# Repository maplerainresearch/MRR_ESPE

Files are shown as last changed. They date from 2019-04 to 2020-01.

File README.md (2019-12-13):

# MRR_ESPE
## A 3D printer control board based on ESP32

This is a 3D printer control board based on the ESP32 microcontroller, which comes with built-in WiFi and BlueTooth.

**Current version: v0.5rev1**<br>

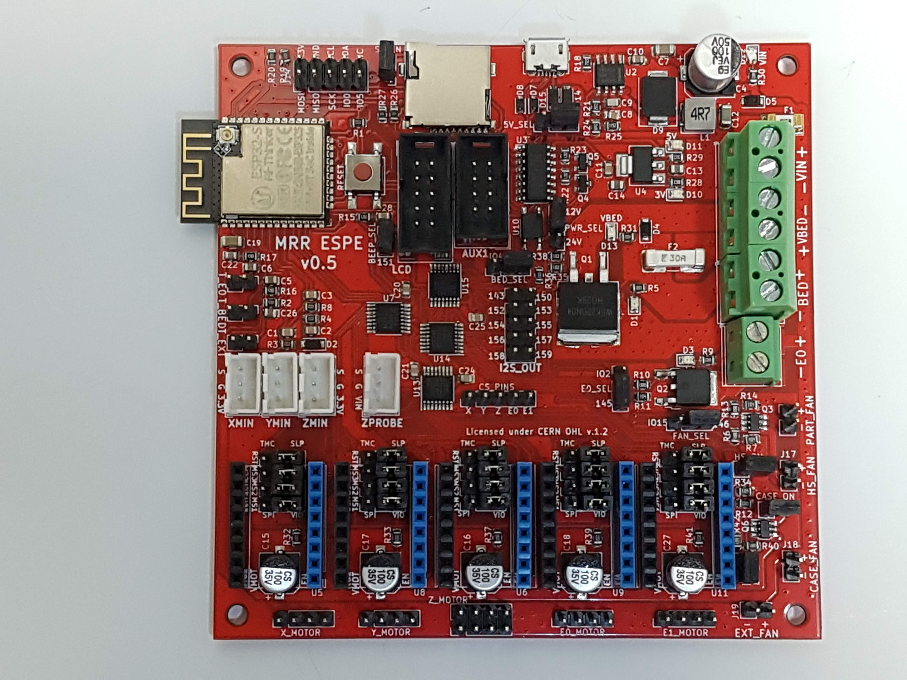
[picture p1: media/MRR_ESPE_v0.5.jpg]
 

Get a pre-launch version at our [store](https://www.maplerain.com/en/products).

Facebook [page](https://www.facebook.com/mrrespx/) <br>
Facebook [group](https://www.facebook.com/groups/mrr.espx.users/) (for discussions, etc.)

Features:
- Able to use up to 5 stepper drivers: X, Y, Z, E0, and E1.
- 12V to 24V input power supply.
- Separate power supply for the heat bed.
- X, Y, and Z min endstops.
- Allows the use of a Z-axis probe, such as an inductive sensor, running on the input supply voltage (12V to 24V).
- Physical size of 102mm by 102mm. Mounting holes are 3.5mm in diameter, with centers 4mm from the edges.
- "RESET" button can be used to reset the board.
- Use of jumper pins for TMC stepper driver connections.
- Firmware controlled fans: case, E0, and EXT. These fans can be controlled by firmware, or they can be in the "always on" mode by shorting the respective jumpers.
- EXP3 connector for Creality LCD controller. 
- AUX1 connector for use with an external host, such as the closed-source MKS TFT32 (**Untested!!**).
- **Note: v0.5 has an issue with AUX1 connector where the RX and TX pins are swapped. To use with controllers like MKS TFT32, dupont connectors will be needed to connect each pin to their corresponding pin separately instead of an IDC cable. The `adapters` directory contains a simple AUX1 adapter board that fixes this issue.**

# Firmware

Marlin 2.0 has added support for ESP32, including the use of I2S to drive motor steppers. This board was based on the pins definition file pins_ESP32.h with some modifications based on MRR ESPA. <br>
In addition, [Luc](https://github.com/luc-github) has been working on a Marlin fork which incorporates part of his ESP3D webUI into Marlin itself.<br>

**Note: Due to timer issues with the I2S stream, babystepping will trigger board reset.**<br>
Note: Marlin's linear advance feature does not work with the I2S stepper stream.<br>

## Flashing firmware

- You should be able to flash firmware through the USB port. Depending on your operating system, you may need to install drivers for the CH340. Please use Google or another search engine to find the right CH340 driver for your operating system.
- To flash firmware by directly connecting to TX/RX pins, you will need to connect IO0 to GND, then reboot (press "BOOT" button) to enter flash mode. After flashing the firmware, disconnect IO0 from GND, and press "BOOT" button again to reboot into normal mode.
- Use a baud rate of 115200.

# Jumpers

- 5V_SEL: Connect to VIN for normal operation; only short (close) this jumper to VUSB if you need to power the board via USB. Note: Powering the board with both PSU and USB may cause unstable operation during heating.
- PWR_SEL: Connect the middle pin PWR_SEL to pin labeled "12V" if using 12V; connect PWR_SEL to pin labeled "24V" if using 24V.
- CASE_ON: Leave open for firmware-controlled case fan; short (close) this jumper for case fan to be always on.
- E0_ON: Leave open for firmware-controlled E0 hotend fan; short (close) this jumper for E0 hotend fan to be always on.
- EXT_ON: Leave open for firmware-controlled extra fan (if used); short (close) this jumper for extra fan to be always on.
- Stepper driver jumpers:
  - MS1: VIO to set high; SPI if using TMC SPI mode
  - MS2: VIO to set high; SPI if using TMC SPI mode
  - MS3: VIO to set high; SPI if using TMC SPI mode
  - RST: SLP if using A4988/DRV8825; SPI if using TMC SPI mode
  - Note: Due to a lack of input pins on the ESP32, UART mode is not supported.

# Pins

See separate PIN_DEF.txt file.
Note: I2S pin 151 labeled as `152` on v0.5 board.

# License
Released under CERN Open Hardware Licence v1.2. See LICENSE.txt for details.

## Warning

- This product uses high currents which may cause fires. Use with caution.
- Do not use input voltages higher than 24V. Input current must not exceed 15A.
- Do not attempt to use more than 15A for the heated bed. While the MOSFET is capable of such currents, the connectors are not. If you need more than 15A, use an external MOSFET. In any case, it is highly recommended to use an external MOSFET for the heated bed to avoid drawing high currents through this product.
- If using a current of more than 10A for the heated bed, it is highly recommended to provide active cooling for the board as the MOSFET and adjacent areas can get very hot due to the high current.
- The underside of the board has PCB traces which are exposed for better cooling. These traces may be carrying high currents and can get very hot. DO NOT touch them, and DO NOT allow these traces to come into contact with metal or other conductive materials.
- Do not attempt to use more than 5A for the hot end. While the MOSFET is capable of such currents, the connectors are not. If you need more than 5A, use an external MOSFET.
- The fan outputs can safely drive up to 0.25A, which is more than enough for most cooling fans. Active cooling of the MOSFETs is recommended for driving currents up to 1A; without active cooling, the MOSFETs can get unduly hot when driving more than 0.25A.
- Do not reverse polarity.
- The breakout and endstop pins are rated for 3.3V, which is the voltage the ESP32 operates at. Attempting to feed inputs above 3.3V to these pins may damage the board.
- It is recommended to power the board only via USB (i.e. turn off PSU power supply) when flashing the board.
- This is still a work in progress. It is recommended not to attempt production using this schematic, although it has been extensively tested.

## Disclaimer

This product is provided as-is. While care has been taken to design a safe product, it is the user's responsibility to make sure precautions are taken to prevent damage or injury when using this product. This includes adhering to all warnings provided. By using this product, the user accepts responsibility to bear all liabilities from any damage or injury arising from the use of this product.

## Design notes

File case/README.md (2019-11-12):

# Cases for MRR ESPE

There are three versions:
1. Basic: Skeleton version, with a simple base, and a top that allows a 40mm fan to be fitted. Standoffs (at least 25mm; more if using stepper drivers with higher heat sinks) are needed.
2. Small: A small, almost enclosed case with a top that allows a 80mm fan to be fitted.
3. Normal: A slightly larger enclosed case, with two types of tops (either a 80mm fan, or two 40mm fans).

There are also covers for 40mm and 80mm fans.

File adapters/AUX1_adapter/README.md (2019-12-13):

# AUX1 adapter
## Fixes issue with AUX1 port on MRR ESPE v0.5

This adapter board fixes MRR ESPE v0.5's issue with the TX/RX pins being swapped on the AUX1 connector.

Simply use an IDC cable to connect AUX1_BRD to the AUX1 connector on the board. Then connect AUX1_SCRN to the screen (such as MKS TFT32).

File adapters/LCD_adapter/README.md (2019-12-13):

# EXP3 to EXP1/2 adapter
## Adapter to allow use of RepRap full graphics smart controller

This adapter allows the MRR ESPE to use generic LCD12864 controllers (officially the RepRap full graphics smart controller).

To do so, connect EXP3_BRD to the LCD connector on the MRR ESPE. Then, connect EXP1 and EXP2 on the adapter to EXP1 and EXP2 on the controller. (Optional: Connect D5, D6, D7 to unused native ESP32 pins on the MRR ESPE, like IO2, IO4, and IO15. Then define `LCD_PINS_D5`, `LCD_PINS_D6`, and `LCD_PINS_D7` in `pins_MRR_ESPE.h`. The KILL pin is also optional.)

If you want to use the SD card on the controller:
1. Remove SD_EN jumper on the MRR ESPE board.
2. Use jumper wires to connect SCK, MISO, and MOSI from the adapter to the respective pins on the board.
3. Connect SS on the adapter to IO5 on the board.
4. Optional: Connect DET to an unused pin on the board. You will need to edit `pins_MRR_ESPE.h` to define the `SD_DETECT_PIN`.

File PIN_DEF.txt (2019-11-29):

Pin Definitions for MRR ESPE
----------------------------

ESP32 pins
0:  BTN_EN1
1:  TX
2:  unused (or HEATER_0_PIN)
3:  RX
4:  unused (or HEATER_BED_PIN)
5:  SS
12: BTN_EN2
13: LCD_PINS_RS
14: BTN_ENC
15: unused (or FAN_PIN)
16: LCD_PINS_D4
17: LCD_PINS_ENABLE
18: SCK
19: MISO
21: SDA
22: SCL
23: MOSI
25: I2S_BCK
26: I2S_WS
27: I2S_DATA
32: Y_MIN_PIN
33: Z_MIN_PIN
34: TEMP_1_PIN
35: X_MIN_PIN
36 (VP): TEMP_E0_PIN
39 (VN): TEMP_BED_PIN

74HC595 (I2S) pins
128: X_ENABLE_PIN
129: X_STEP_PIN
130: X_DIR_PIN
131: Y_ENABLE_PIN
132: Y_STEP_PIN
133: Y_DIR_PIN
134: Z_ENABLE_PIN
135: Z_STEP_PIN
136: Z_DIR_PIN
137: E0_ENABLE_PIN
138: E0_STEP_PIN
139: E0_DIR_PIN
140: E1_ENABLE_PIN
141: E1_STEP_PIN
142: E1_DIR_PIN
143: unused
144: HEATER_BED_PIN
145: HEATER_0_PIN
146: FAN_PIN
147: CONTROLLER_FAN_PIN
148: E0_AUTO_FAN_PIN
149: FAN1_PIN
150: unused
151: BEEPER_PIN
152: unused
153: unused
154: unused
155: unused
156: unused
157: unused
158: unused
159: unused

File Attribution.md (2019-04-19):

# Attribution

Schematics of the following boards were referenced in the design of MRR ESPE:
- [SMART RAMPS 1.42](https://reprap.org/wiki/SMART_RAMPS)
- [ESP32Controller](https://github.com/simon-jouet/ESP32Controller)
- [STEVAL-3DP001V1](https://www.st.com/en/evaluation-tools/steval-3dp001v1.html)
- [Duet 3D Printer Controller](https://github.com/T3P3/Duet)
- [Smoothieboard](https://github.com/Smoothieware/Smoothieboard)
- [Arduino UNO R3](https://www.arduino.cc/en/uploads/Main/Arduino_Uno_Rev3-schematic.pdf)
- [Little-Driver](https://github.com/Digital-Sqrt/Little-Driver)

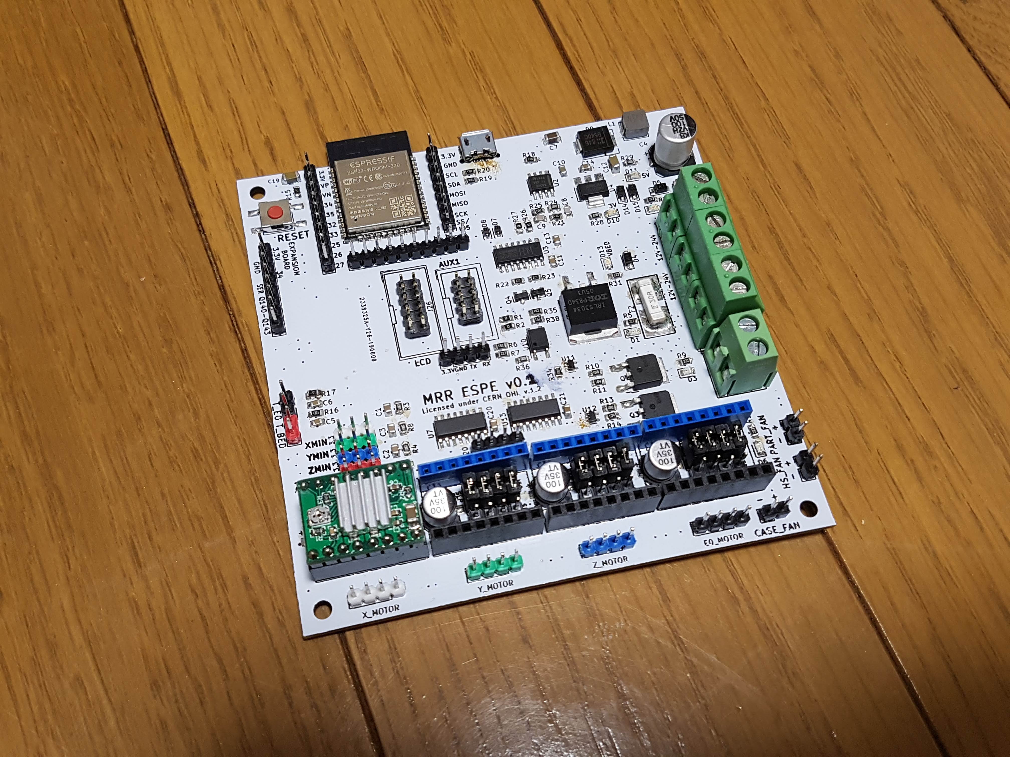
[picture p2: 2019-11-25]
media/MRR_ESPE_v0.2.jpg

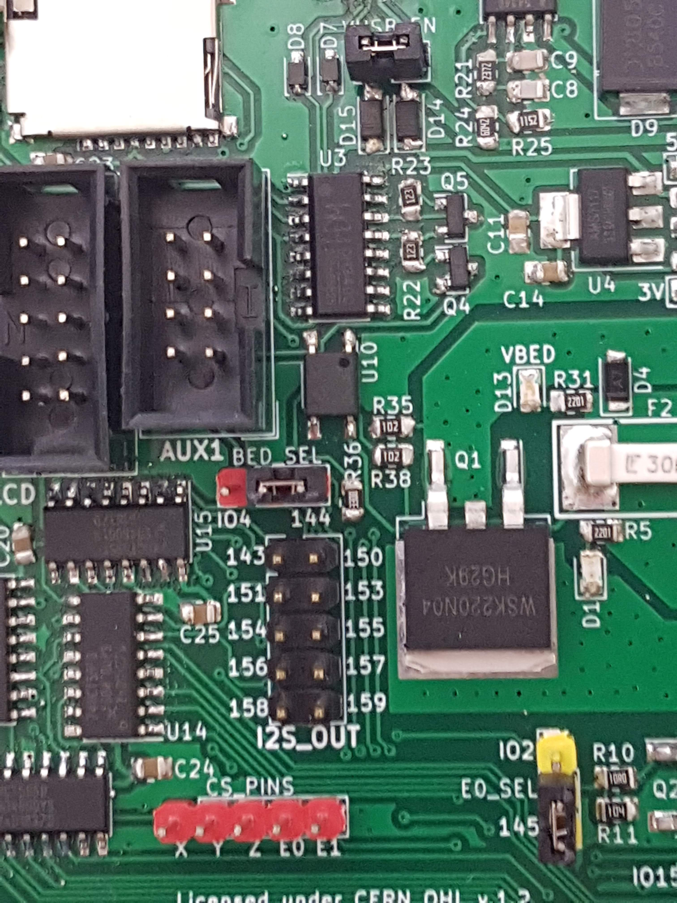
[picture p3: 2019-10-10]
media/ESPE PWM select bed.jpg

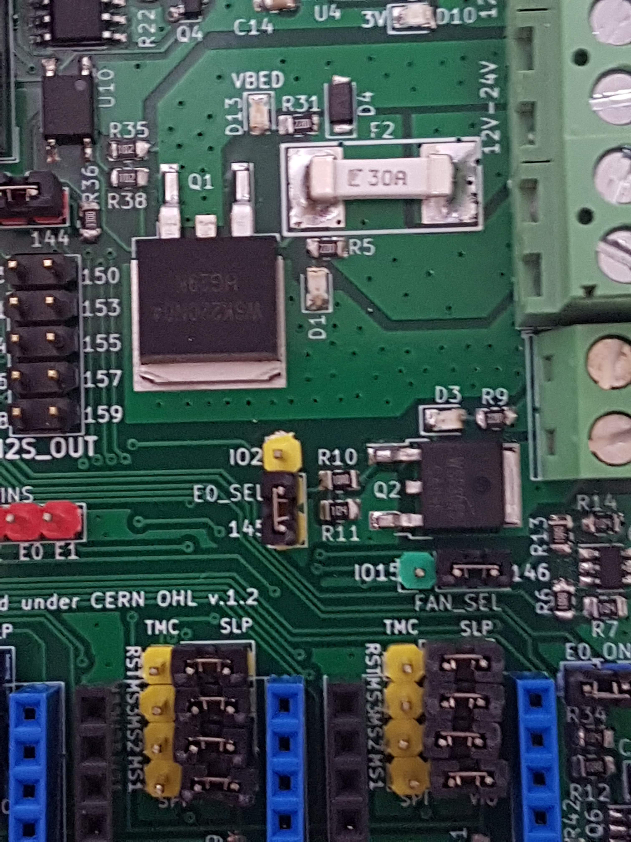
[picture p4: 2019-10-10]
media/ESPE PWM select E0.jpg

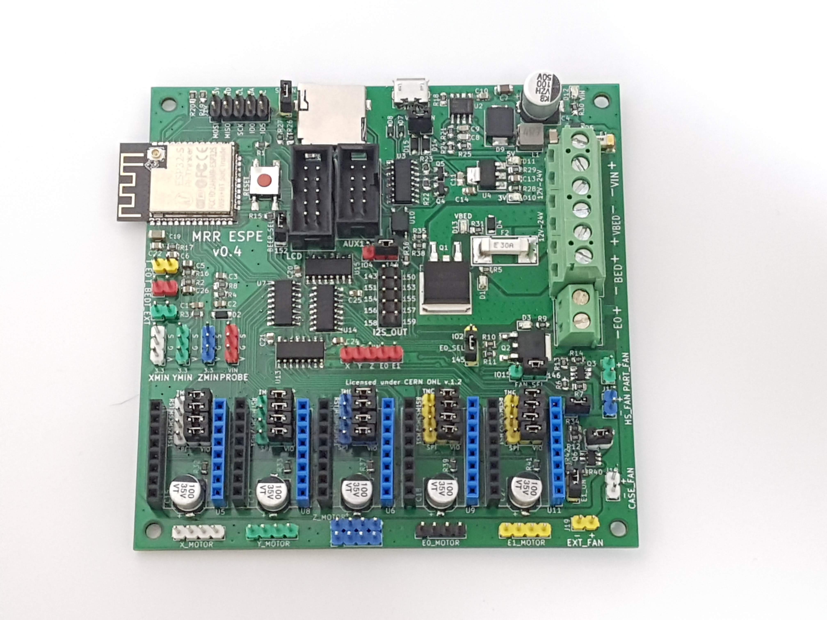
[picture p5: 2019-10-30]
media/MRR_ESPE_v0.4.jpg

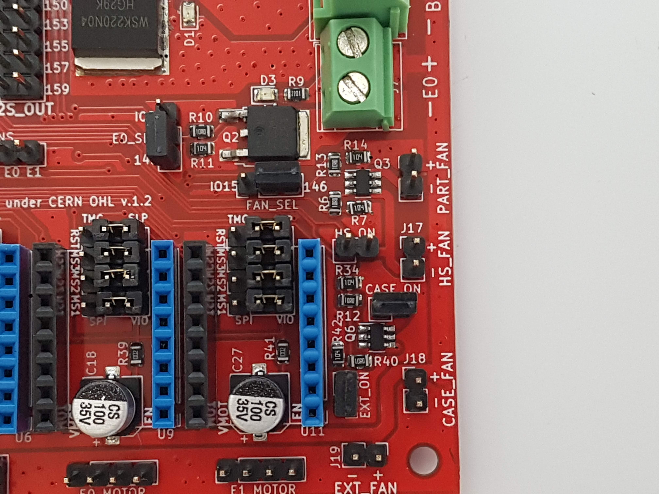
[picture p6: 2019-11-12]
media/ESPE_fan_jumpers.jpg

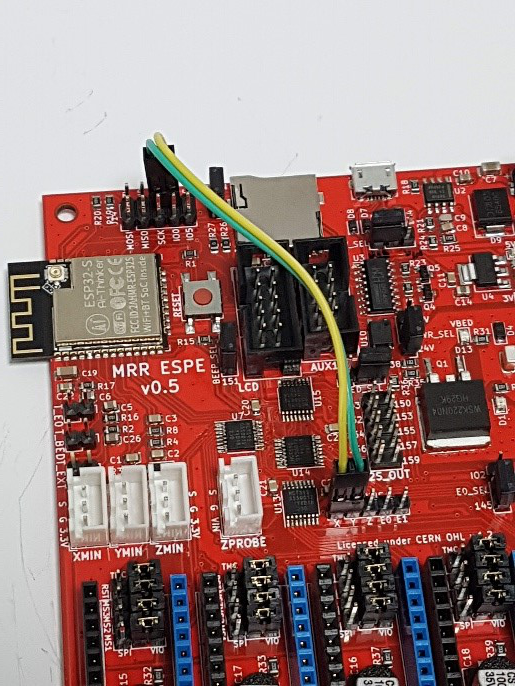
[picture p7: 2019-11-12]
media/ESPE_TMC_jumper_cable.jpg

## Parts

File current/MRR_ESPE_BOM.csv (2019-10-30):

Reference | Value | Footprint | Datasheet | LCSC Part Number | Manufacturer | Mfg part no.
U1 | ESP32-WROOM-32D | RF_Module:ESP32-WROOM-32 | https://www.espressif.com/sites/default/files/documentation/esp32-wroom-32d_esp32-wroom-32u_datasheet_en.pdf | C95209 | Espressif Systems | ESP32-WROOM-32
J9 | PWR_IN | TerminalBlock_Phoenix:TerminalBlock_Phoenix_MKDS-3-4-5.08_1x04_P5.08mm_Horizontal | ~ | C90087 | Phoenix Contact | MKDS3/4-5.08
F1 | 15A 2410 | projfp:Littelfuse_0451 | Bel 0679H9150-01 | C44480 | Littelfuse | 0451015.MRL
F2 | 30A 3912 | projfp:Littelfuse_0456 | Bel 0678H9300-02 | C187558 | Littelfuse | 0456030.ER
D4 | 1N4007W | projfp:D_SOD-123F | http://www.vishay.com/docs/88503/1n4001.pdf | C108803 | Shandong Jingdao Microelectronics | 1N4007W
D5 | 1N4007W | projfp:D_SOD-123F | http://www.vishay.com/docs/88503/1n4001.pdf | C108803 | Shandong Jingdao Microelectronics | 1N4007W
U2 | TPS54340DDA | Package_SO:TI_SO-PowerPAD-8_ThermalVias | http://www.ti.com/lit/ds/symlink/tps54340.pdf | C45886 | Texas Instruments | TPS54340DDAR
C10 | 100nF50V | Capacitor_SMD:C_0805_2012Metric | ~ | C161260 | Murata Electronics | GCM21BR71H104KA37L
C7 | 4.7uF50V | Capacitor_SMD:C_1206_3216Metric | ~ | C307575 | Samsung Electro-Mechanics | CL31B475KBHNFNE
C4 | 100uF50V | Capacitor_SMD:CP_Elec_8x10 | ~ | C176665 | Lelon | VEJ101M1HTR-0810
L1 | 4.7uH4.5A | projfp:SMMS0530 | ~ | C181722 | Shun Xiang Nuo Elec | SMMS0530-4R7M
D9 | B540C-13-F | projfp:D_SMC | ~ | C72264 | Diodes Incorporated | B540C-13-F
R24 | 60.4K | Resistor_SMD:R_0805_2012Metric | ~ | C273994 | YAGEO | RC0805FR-0760K4L
R25 | 11.5K | Resistor_SMD:R_0805_2012Metric | ~ | C17418 | Uniroyal Elec | 0805W8F1152T5E
C12 | 47uF10V | Capacitor_SMD:C_1206_3216Metric | ~ | C92821 | Taiyo Yuden | LMK316BJ476ML-T
C8 | 820pF50V | Capacitor_SMD:C_0805_2012Metric | ~ | C152862 | Walsin Tech Corp | 0805B821K500CT
R21 | 23.7K | Resistor_SMD:R_0805_2012Metric | ~ | C170848 | Walsin Tech Corp | WR08X2372FTL
C9 | 56pF50V | Capacitor_SMD:C_0805_2012Metric | ~ | C296102 | Walsin Tech Corp | 0805N560J500CT
R18 | 73.2K | Resistor_SMD:R_0805_2012Metric | ~ | C170958 | Walsin Tech Corp | WR08X7322FTL
U4 | AMS1117-3.3 | Package_TO_SOT_SMD:SOT-223-3_TabPin2 | http://www.advanced-monolithic.com/pdf/ds1117.pdf | C6186 | Advanced Monolithic Systems | AMS1117-3.3
C14 | 47uF6.3V | Capacitor_SMD:C_0805_2012Metric | ~ | C87159 | Taiyo Yuden | JMK212BJ476MG-T
C13 | 47uF6.3V | Capacitor_SMD:C_0805_2012Metric | ~ | C87159 | Taiyo Yuden | JMK212BJ476MG-T
R28 | 220R | Resistor_SMD:R_0805_2012Metric | ~ | C17557 | Uniroyal Elec | 0805W8F2200T5E
D10 | LED_3V | projfp:LED_0805 | ~ | C73548 | Everlight Elec | 17-21SYGC/S530-E2/TR8
R29 | 330R | Resistor_SMD:R_0805_2012Metric | ~ | C17630 | Uniroyal Elec | 0805W8F3300T5E
R30 | 2.2K | Resistor_SMD:R_0805_2012Metric | ~ | C17520 | Uniroyal Elec | 0805W8F2201T5E
R31 | 2.2K | Resistor_SMD:R_0805_2012Metric | ~ | C17520 | Uniroyal Elec | 0805W8F2201T5E
D11 | LED_5V | projfp:LED_0805 | ~ | C73548 | Everlight Elec | 17-21SYGC/S530-E2/TR8
D12 | LED_VIN | projfp:LED_0805 | ~ | C72035 | Everlight Elec | 17-21/BHC-XL2M2TY/3T
D13 | LED_VBED | projfp:LED_0805 | ~ | C72035 | Everlight Elec | 17-21/BHC-XL2M2TY/3T
R26 | 0R | Resistor_SMD:R_0805_2012Metric | ~ | C17477 | Uniroyal Elec | 0805W8F0000T5E
R27 | 0R | Resistor_SMD:R_0805_2012Metric | ~ | C17477 | Uniroyal Elec | 0805W8F0000T5E
C11 | 1nF16V | Capacitor_SMD:C_0805_2012Metric | ~ | C52278 | Guangdong Fenghua Advanced Tech | 0805B103K500NT
J16 | USB_B_Micro | Connector_USB:USB_Micro-B_Molex-105017-0001 | ~ | C136000 | MOLEX | 105017-0001
D7 | PESD5V0S1BA | projfp:D_SOD-323 | ~ | C19224 | Nexperia | PESD5V0S1BA,115
D8 | PESD5V0S1BA | projfp:D_SOD-323 | ~ | C19224 | Nexperia | PESD5V0S1BA,115
Q4 | S9014 | Package_TO_SOT_SMD:SOT-23 | http://www.onsemi.com/pub_link/Collateral/2N3055-D.PDF | C181164 | Guangdong Hottech | S9014
Q5 | S9014 | Package_TO_SOT_SMD:SOT-23 | http://www.onsemi.com/pub_link/Collateral/2N3055-D.PDF | C181164 | Guangdong Hottech | S9014
R22 | 12K | Resistor_SMD:R_0805_2012Metric | ~ | C17444 | Uniroyal Elec | 0805W8F1202T5E
R23 | 12K | Resistor_SMD:R_0805_2012Metric | ~ | C17444 | Uniroyal Elec | 0805W8F1202T5E
Q1 | IRLS3034PBF | Package_TO_SOT_SMD:TO-263-2 | ~
Q2 | IRLR8743TRPBF | Package_TO_SOT_SMD:TO-252-2 | ~
R5 | 2.2K | Resistor_SMD:R_0805_2012Metric | ~ | C17520 | Uniroyal Elec | 0805W8F2201T5E
D1 | LED_BED | projfp:LED_0805 | ~ | C72037 | Everlight Elec | 17-21SURC/S530-A3/TR8
J3 | BED | TerminalBlock_Phoenix:TerminalBlock_Phoenix_MKDS-3-2-5.08_1x02_P5.08mm_Horizontal | ~ | C89120 | Phoenix Contact | MKDS3/2-5.08
R9 | 2.2K | Resistor_SMD:R_0805_2012Metric | ~ | C17520 | Uniroyal Elec | 0805W8F2201T5E
J7 | E0 | TerminalBlock_Phoenix:TerminalBlock_Phoenix_MKDS-1,5-2-5.08_1x02_P5.08mm_Horizontal | ~ | C91153 | Phoenix Contact | MKDSN1.5/2-5.08
R10 | 10R | Resistor_SMD:R_0805_2012Metric | ~ | C17415 | Uniroyal Elec | 0805W8F100JT5E
R11 | 100K | Resistor_SMD:R_0805_2012Metric | ~ | C149504 | Uniroyal Elec | 0805W8F1003T5E
R13 | 10R | Resistor_SMD:R_0805_2012Metric | ~ | C17415 | Uniroyal Elec | 0805W8F100JT5E
R14 | 100K | Resistor_SMD:R_0805_2012Metric | ~ | C149504 | Uniroyal Elec | 0805W8F1003T5E
J10 | PART_FAN | Connector_PinHeader_2.54mm:PinHeader_1x02_P2.54mm_Vertical | ~ | C124375 | Shenzhen Cankemeng | C124375
U8 | Pololu_board | Module:Pololu_Breakout-16_15.2x20.3mm |  | C27438 | Boom Precision Elec | x2
U5 | Pololu_board | Module:Pololu_Breakout-16_15.2x20.3mm |  | C27438 | Boom Precision Elec | x2
J21 | X_MOTOR | Connector_PinHeader_2.54mm:PinHeader_1x04_P2.54mm_Vertical | ~ | C124378 | Shenzhen Cankemeng | C124378
C15 | 100uF35V | Capacitor_SMD:CP_Elec_6.3x7.7 | ~ | C97811 | Semtech | CS1V101M-CRE77
U6 | Pololu_board | Module:Pololu_Breakout-16_15.2x20.3mm |  | C27438 | Boom Precision Elec | x2
U9 | Pololu_board | Module:Pololu_Breakout-16_15.2x20.3mm |  | C27438 | Boom Precision Elec | x2
C16 | 100uF35V | Capacitor_SMD:CP_Elec_6.3x7.7 | ~ | C97811 | Semtech | CS1V101M-CRE77
C17 | 100uF35V | Capacitor_SMD:CP_Elec_6.3x7.7 | ~ | C97811 | Semtech | CS1V101M-CRE77
C18 | 100uF35V | Capacitor_SMD:CP_Elec_6.3x7.7 | ~ | C97811 | Semtech | CS1V101M-CRE77
J23 | Y_MOTOR | Connector_PinHeader_2.54mm:PinHeader_1x04_P2.54mm_Vertical | ~ | C124378 | Shenzhen Cankemeng | C124378
J24 | E0_MOTOR | Connector_PinHeader_2.54mm:PinHeader_1x04_P2.54mm_Vertical | ~ | C124378 | Shenzhen Cankemeng | C124378
J22 | Z_MOTOR | Connector_PinHeader_2.54mm:PinHeader_2x04_P2.54mm_Vertical | ~ | C124386 | Shenzhen Cankemeng | C124386
D3 | LED_E0 | projfp:LED_0805 | ~ | C72037 | Everlight Elec | 17-21SURC/S530-A3/TR8
J12 | T_BED | Connector_PinHeader_2.54mm:PinHeader_1x02_P2.54mm_Vertical | ~ | C124375 | Shenzhen Cankemeng | C124375
R16 | 4.7K | Resistor_SMD:R_0805_2012Metric | ~ | C17673 | Uniroyal Elec | 0805W8F4701T5E
C5 | 22uF6.3V | Capacitor_SMD:C_0805_2012Metric | ~ | C5674 | Samsung Electro-Mechanics | CL21A226MQQNNNE
J13 | T_E0 | Connector_PinHeader_2.54mm:PinHeader_1x02_P2.54mm_Vertical | ~ | C124375 | Shenzhen Cankemeng | C124375
R17 | 4.7K | Resistor_SMD:R_0805_2012Metric | ~ | C17673 | Uniroyal Elec | 0805W8F4701T5E
C6 | 22uF6.3V | Capacitor_SMD:C_0805_2012Metric | ~ | C5674 | Samsung Electro-Mechanics | CL21A226MQQNNNE
J1 | X_MIN | Connector_JST:JST_XH_B03B-XH-A_1x03_P2.50mm_Vertical | ~ | C144394 | JST Sales America | B3B-XH-A(LF)(SN)
R3 | 10K | Resistor_SMD:R_0805_2012Metric | ~ | C38522 | Uniroyal Elec | 0805W8F1002T5E
C1 | 100nF25V | Capacitor_SMD:C_0805_2012Metric | ~ | C128353 | Walsin Tech Corp | 0805B104K250
J5 | Y_MIN | Connector_JST:JST_XH_B03B-XH-A_1x03_P2.50mm_Vertical | ~ | C144394 | JST Sales America | B3B-XH-A(LF)(SN)
R8 | 10K | Resistor_SMD:R_0805_2012Metric | ~ | C38522 | Uniroyal Elec | 0805W8F1002T5E
C3 | 100nF25V | Capacitor_SMD:C_0805_2012Metric | ~ | C128353 | Walsin Tech Corp | 0805B104K250
J2 | Z_MIN | Connector_JST:JST_XH_B03B-XH-A_1x03_P2.50mm_Vertical | ~ | C144394 | JST Sales America | B3B-XH-A(LF)(SN)
R4 | 10K | Resistor_SMD:R_0805_2012Metric | ~ | C38522 | Uniroyal Elec | 0805W8F1002T5E
C2 | 100nF25V | Capacitor_SMD:C_0805_2012Metric | ~ | C128353 | Walsin Tech Corp | 0805B104K250
J6 | Z_PROBE | Connector_JST:JST_XH_B03B-XH-A_1x03_P2.50mm_Vertical | ~ | C144394 | JST Sales America | B3B-XH-A(LF)(SN)
D2 | 1N4148W | projfp:D_SOD-123 | https://www.vishay.com/docs/85748/1n4148w.pdf | C81598 | Semtech | 1N4148W
R15 | 12K | Resistor_SMD:R_0805_2012Metric | ~ | C17444 | Uniroyal Elec | 0805W8F1202T5E
SW1 | RESET | projfp:6x6mmTactileSwitch |  | C83206 | Korean Hroparts Elec | K2-6639SP-C4SC-04
J15 | AUX1 | Connector_IDC:IDC-Header_2x04_P2.54mm_Vertical | ~ | C9135 | Boom Precision Elec | C9135
R19 | 4.7K | Resistor_SMD:R_0805_2012Metric | ~ | C17673 | Uniroyal Elec | 0805W8F4701T5E
R20 | 4.7K | Resistor_SMD:R_0805_2012Metric | ~ | C17673 | Uniroyal Elec | 0805W8F4701T5E
H1 | MountingHole | MountingHole:MountingHole_3.2mm_M3_DIN965 | ~
H2 | MountingHole | MountingHole:MountingHole_3.2mm_M3_DIN965 | ~
H3 | MountingHole | MountingHole:MountingHole_3.2mm_M3_DIN965 | ~
H4 | MountingHole | MountingHole:MountingHole_3.2mm_M3_DIN965 | ~
JP1 | X_MS1 | Connector_PinHeader_2.54mm:PinHeader_1x03_P2.54mm_Vertical | ~ | C124376 | Shenzhen Cankemeng | C124376
JP5 | X_MS2 | Connector_PinHeader_2.54mm:PinHeader_1x03_P2.54mm_Vertical | ~ | C124376 | Shenzhen Cankemeng | C124376
JP9 | X_MS3 | Connector_PinHeader_2.54mm:PinHeader_1x03_P2.54mm_Vertical | ~ | C124376 | Shenzhen Cankemeng | C124376
JP13 | X_RST | Connector_PinHeader_2.54mm:PinHeader_1x03_P2.54mm_Vertical | ~ | C124376 | Shenzhen Cankemeng | C124376
J20 | CS_PINS | Connector_PinHeader_2.54mm:PinHeader_1x05_P2.54mm_Vertical | ~ | C124379 | Shenzhen Cankemeng | C124379
JP2 | Y_MS1 | Connector_PinHeader_2.54mm:PinHeader_1x03_P2.54mm_Vertical | ~ | C124376 | Shenzhen Cankemeng | C124376
JP6 | Y_MS2 | Connector_PinHeader_2.54mm:PinHeader_1x03_P2.54mm_Vertical | ~ | C124376 | Shenzhen Cankemeng | C124376
JP10 | Y_MS3 | Connector_PinHeader_2.54mm:PinHeader_1x03_P2.54mm_Vertical | ~ | C124376 | Shenzhen Cankemeng | C124376
JP14 | Y_RST | Connector_PinHeader_2.54mm:PinHeader_1x03_P2.54mm_Vertical | ~ | C124376 | Shenzhen Cankemeng | C124376
JP3 | Z_MS1 | Connector_PinHeader_2.54mm:PinHeader_1x03_P2.54mm_Vertical | ~ | C124376 | Shenzhen Cankemeng | C124376
JP7 | Z_MS2 | Connector_PinHeader_2.54mm:PinHeader_1x03_P2.54mm_Vertical | ~ | C124376 | Shenzhen Cankemeng | C124376
JP11 | Z_MS3 | Connector_PinHeader_2.54mm:PinHeader_1x03_P2.54mm_Vertical | ~ | C124376 | Shenzhen Cankemeng | C124376
JP15 | Z_RST | Connector_PinHeader_2.54mm:PinHeader_1x03_P2.54mm_Vertical | ~ | C124376 | Shenzhen Cankemeng | C124376
JP4 | E0_MS1 | Connector_PinHeader_2.54mm:PinHeader_1x03_P2.54mm_Vertical | ~ | C124376 | Shenzhen Cankemeng | C124376
JP8 | E0_MS2 | Connector_PinHeader_2.54mm:PinHeader_1x03_P2.54mm_Vertical | ~ | C124376 | Shenzhen Cankemeng | C124376
JP12 | E0_MS3 | Connector_PinHeader_2.54mm:PinHeader_1x03_P2.54mm_Vertical | ~ | C124376 | Shenzhen Cankemeng | C124376
JP16 | E0_RST | Connector_PinHeader_2.54mm:PinHeader_1x03_P2.54mm_Vertical | ~ | C124376 | Shenzhen Cankemeng | C124376
U3 | CH340C | Package_SO:SOIC-16_3.9x9.9mm_P1.27mm | http://www.datasheet5.com/pdf-local-2195953 | C84681 | Jiangsu Qin Heng | CH340C
J4 | Micro_SD_Card_China | projfp:Conn_uSDcard |  | C111196 | SOFNG | TF-15×15
C19 | 100uF6.3V | Capacitor_SMD:C_1206_3216Metric | ~ | C15008 | Samsung Electro-Mechanics | CL31A107MQHNNNE
R38 | 1K | Resistor_SMD:R_0805_2012Metric | ~ | C17513 | Uniroyal Elec | 0805W8F1001T5E
R35 | 1K | Resistor_SMD:R_0805_2012Metric | ~ | C17513 | Uniroyal Elec | 0805W8F1001T5E
U10 | TLP182 | Package_SO:MFSOP6-4_4.4x3.6mm_P1.27mm | https://toshiba.semicon-storage.com/info/docget.jsp?did=11793&prodName=TLP184 | C96457 | TOSHIBA | TLP182(GB-TPL,E
R36 | 330R | Resistor_SMD:R_0805_2012Metric | ~ | C17630 | Uniroyal Elec | 0805W8F3300T5E
D14 | 1N5819W | Diode_SMD:D_SOD-123 | http://www.vishay.com/docs/88525/1n5817.pdf | C169540 | Shandong Jingdao Microelectronics | 1N5819W
D15 | 1N5819W | Diode_SMD:D_SOD-123 | http://www.vishay.com/docs/88525/1n5817.pdf | C169540 | Shandong Jingdao Microelectronics | 1N5819W
U7 | 74HCT595 | Package_SO:TSSOP-16_4.4x5mm_P0.65mm | http://www.ti.com/lit/ds/symlink/sn74hc595.pdf | C152276 | ON Semicon | MC74HCT595ADTR2G
U13 | 74HCT595 | Package_SO:TSSOP-16_4.4x5mm_P0.65mm | http://www.ti.com/lit/ds/symlink/sn74hc595.pdf | C152276 | ON Semicon | MC74HCT595ADTR2G
C20 | 100nF25V | Capacitor_SMD:C_0805_2012Metric | ~ | C128353 | Walsin Tech Corp | 0805B104K250
C21 | 100nF25V | Capacitor_SMD:C_0805_2012Metric | ~ | C128353 | Walsin Tech Corp | 0805B104K250
J26 | EXP3 | Connector_IDC:IDC-Header_2x05_P2.54mm_Vertical | ~ | C5665 | Boom Precision Elec | C5665
U14 | 74HCT595 | Package_SO:TSSOP-16_4.4x5mm_P0.65mm | http://www.ti.com/lit/ds/symlink/sn74hc595.pdf | C152276 | ON Semicon | MC74HCT595ADTR2G
U15 | 74HCT595 | Package_SO:TSSOP-16_4.4x5mm_P0.65mm | http://www.ti.com/lit/ds/symlink/sn74hc595.pdf | C152276 | ON Semicon | MC74HCT595ADTR2G
C24 | 100nF25V | Capacitor_SMD:C_0805_2012Metric | ~ | C128353 | Walsin Tech Corp | 0805B104K250
C25 | 100nF25V | Capacitor_SMD:C_0805_2012Metric | ~ | C128353 | Walsin Tech Corp | 0805B104K250
C22 | 22uF6.3V | Capacitor_SMD:C_0805_2012Metric | ~ | C5674 | Samsung Electro-Mechanics | CL21A226MQQNNNE
C23 | 100nF25V | Capacitor_SMD:C_0805_2012Metric | ~ | C128353 | Walsin Tech Corp | 0805B104K250
R33 | 10K | Resistor_SMD:R_0805_2012Metric | ~ | C38522 | Uniroyal Elec | 0805W8F1002T5E
R32 | 10K | Resistor_SMD:R_0805_2012Metric | ~ | C38522 | Uniroyal Elec | 0805W8F1002T5E
R37 | 10K | Resistor_SMD:R_0805_2012Metric | ~ | C38522 | Uniroyal Elec | 0805W8F1002T5E
R39 | 10K | Resistor_SMD:R_0805_2012Metric | ~ | C38522 | Uniroyal Elec | 0805W8F1002T5E
R1 | 10K | Resistor_SMD:R_0805_2012Metric | ~ | C38522 | Uniroyal Elec | 0805W8F1002T5E
Q6 | WST3392 | Package_TO_SOT_SMD:SOT-23-6_Handsoldering |  | C148366 | Winsok Semicon | WST3392
Q3 | WST3392 | Package_TO_SOT_SMD:SOT-23-6_Handsoldering |  | C148366 | Winsok Semicon | WST3392
J11 | UNUSED | Connector_PinHeader_2.54mm:PinHeader_2x05_P2.54mm_Vertical | ~ | C124387 | Shenzhen Cankemeng | C124387
R12 | 10R | Resistor_SMD:R_0805_2012Metric | ~ | C17415 | Uniroyal Elec | 0805W8F100JT5E
R34 | 100K | Resistor_SMD:R_0805_2012Metric | ~ | C149504 | Uniroyal Elec | 0805W8F1003T5E
J18 | CASE_FAN | Connector_PinHeader_2.54mm:PinHeader_1x02_P2.54mm_Vertical | ~ | C124375 | Shenzhen Cankemeng | C124375
JP23 | CASE_ON | Connector_PinHeader_2.54mm:PinHeader_1x02_P2.54mm_Vertical | ~ | C124375 | Shenzhen Cankemeng | C124375
R6 | 10R | Resistor_SMD:R_0805_2012Metric | ~ | C17415 | Uniroyal Elec | 0805W8F100JT5E
R7 | 100K | Resistor_SMD:R_0805_2012Metric | ~ | C149504 | Uniroyal Elec | 0805W8F1003T5E
J17 | HS_FAN | Connector_PinHeader_2.54mm:PinHeader_1x02_P2.54mm_Vertical | ~ | C124375 | Shenzhen Cankemeng | C124375
JP21 | HS_ON | Connector_PinHeader_2.54mm:PinHeader_1x02_P2.54mm_Vertical | ~ | C124375 | Shenzhen Cankemeng | C124375
R40 | 10R | Resistor_SMD:R_0805_2012Metric | ~ | C17415 | Uniroyal Elec | 0805W8F100JT5E
R42 | 100K | Resistor_SMD:R_0805_2012Metric | ~ | C149504 | Uniroyal Elec | 0805W8F1003T5E
J19 | EXT_FAN | Connector_PinHeader_2.54mm:PinHeader_1x02_P2.54mm_Vertical | ~ | C124375 | Shenzhen Cankemeng | C124375
JP24 | EXT_ON | Connector_PinHeader_2.54mm:PinHeader_1x02_P2.54mm_Vertical | ~ | C124375 | Shenzhen Cankemeng | C124375
J8 | T_EXT | Connector_PinHeader_2.54mm:PinHeader_1x02_P2.54mm_Vertical | ~ | C124375 | Shenzhen Cankemeng | C124375
R2 | 4.7K | Resistor_SMD:R_0805_2012Metric | ~ | C17673 | Uniroyal Elec | 0805W8F4701T5E
C26 | 22uF6.3V | Capacitor_SMD:C_0805_2012Metric | ~ | C5674 | Samsung Electro-Mechanics | CL21A226MQQNNNE
J14 | I2C/SPI | Connector_PinHeader_2.54mm:PinHeader_2x05_P2.54mm_Vertical | ~ | C124387 | Shenzhen Cankemeng | C124387
JP22 | E1_MS1 | Connector_PinHeader_2.54mm:PinHeader_1x03_P2.54mm_Vertical | ~ | C124376 | Shenzhen Cankemeng | C124376
JP25 | E1_MS2 | Connector_PinHeader_2.54mm:PinHeader_1x03_P2.54mm_Vertical | ~ | C124376 | Shenzhen Cankemeng | C124376
JP26 | E1_MS3 | Connector_PinHeader_2.54mm:PinHeader_1x03_P2.54mm_Vertical | ~ | C124376 | Shenzhen Cankemeng | C124376
JP27 | E1_RST | Connector_PinHeader_2.54mm:PinHeader_1x03_P2.54mm_Vertical | ~ | C124376 | Shenzhen Cankemeng | C124376
U11 | Pololu_board | Module:Pololu_Breakout-16_15.2x20.3mm |  | C27438 | Boom Precision Elec | x2
C27 | 100uF35V | Capacitor_SMD:CP_Elec_6.3x7.7 | ~ | C97811 | Semtech | CS1V101M-CRE77
J25 | E1_MOTOR | Connector_PinHeader_2.54mm:PinHeader_1x04_P2.54mm_Vertical | ~ | C124378 | Shenzhen Cankemeng | C124378
JP18 | BED_SEL | Connector_PinHeader_2.54mm:PinHeader_1x03_P2.54mm_Vertical | ~ | C124376 | Shenzhen Cankemeng | C124376
JP20 | E0_SEL | Connector_PinHeader_2.54mm:PinHeader_1x03_P2.54mm_Vertical | ~ | C124376 | Shenzhen Cankemeng | C124376
JP19 | FAN_SEL | Connector_PinHeader_2.54mm:PinHeader_1x03_P2.54mm_Vertical | ~ | C124376 | Shenzhen Cankemeng | C124376
JP17 | BEEP_SEL | Connector_PinHeader_2.54mm:PinHeader_1x02_P2.54mm_Vertical | ~ | C124375 | Shenzhen Cankemeng | C124375
R41 | 10K | Resistor_SMD:R_0805_2012Metric | ~ | C38522 | Uniroyal Elec | 0805W8F1002T5E
JP29 | SD_EN | Connector_PinHeader_2.54mm:PinHeader_1x02_P2.54mm_Vertical | ~ | C124375 | Shenzhen Cankemeng | C124375
JP30 | PWR_SEL | Connector_PinHeader_2.54mm:PinHeader_1x03_P2.54mm_Vertical | ~ | C124376 | Shenzhen Cankemeng | C124376
C28 | 100nF25V | Capacitor_SMD:C_0805_2012Metric | ~ | C128353 | Walsin Tech Corp | 0805B104K250
JP28 | 5V_SEL | Connector_PinHeader_2.54mm:PinHeader_1x03_P2.54mm_Vertical | ~ | C124376 | Shenzhen Cankemeng | C124376

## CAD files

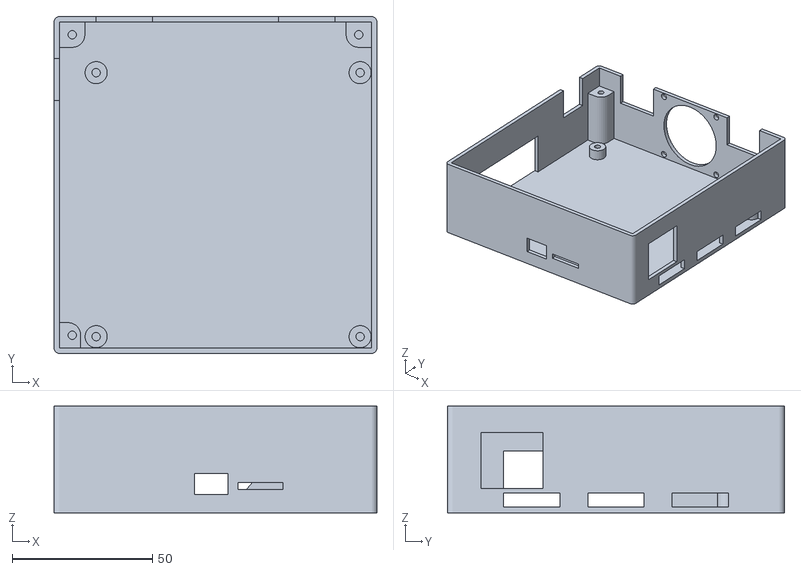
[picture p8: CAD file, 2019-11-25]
case/ESPE_bottom_small.stl
115.0 x 120.0 x 38.0

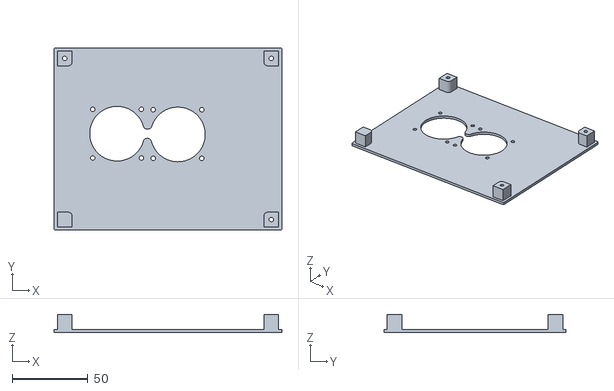
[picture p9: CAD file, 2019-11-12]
case/ESPE_top_40mm_fan.stl
150.0 x 120.0 x 12.0

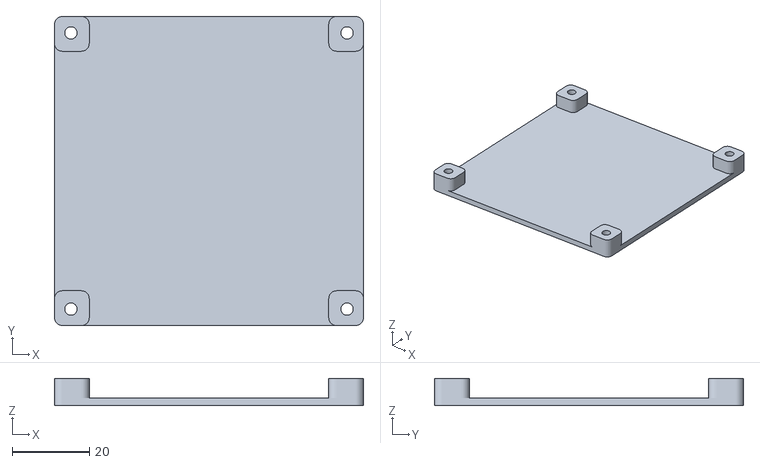
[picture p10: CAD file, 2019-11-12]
case/80mm_fan_cover.stl
80.0 x 80.0 x 7.00

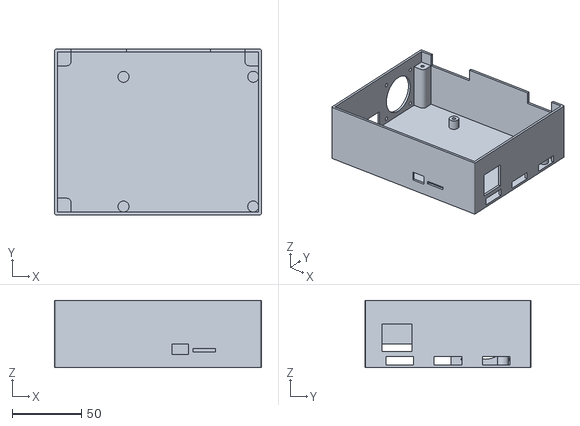
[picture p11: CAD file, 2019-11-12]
case/ESPE_bottom.stl
150.0 x 120.0 x 48.6

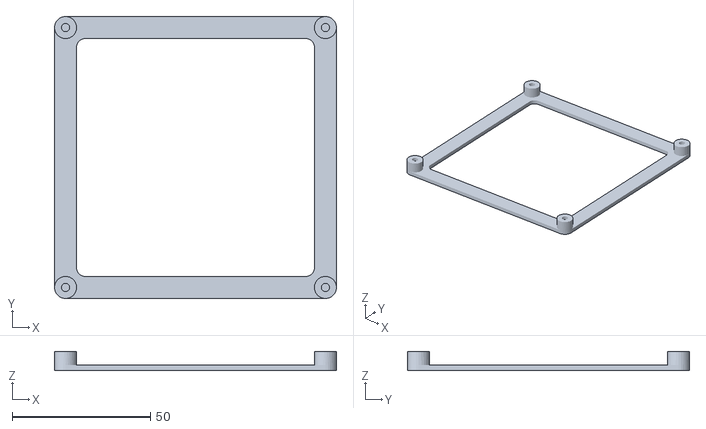
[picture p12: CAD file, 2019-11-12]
case/ESPE_basic_bottom.stl
102.0 x 102.0 x 7.00

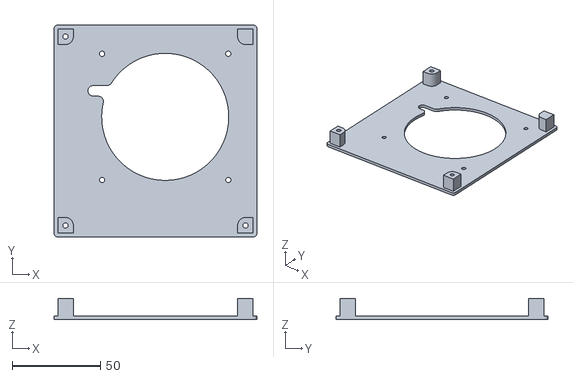
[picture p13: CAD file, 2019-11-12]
case/ESPE_top_small_80mm_fan.stl
115.0 x 120.0 x 12.0

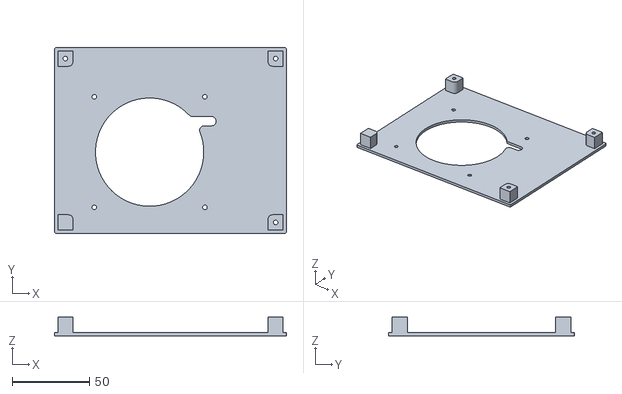
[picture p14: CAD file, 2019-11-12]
case/ESPE_top_80mm_fan.stl
150.0 x 120.0 x 12.0

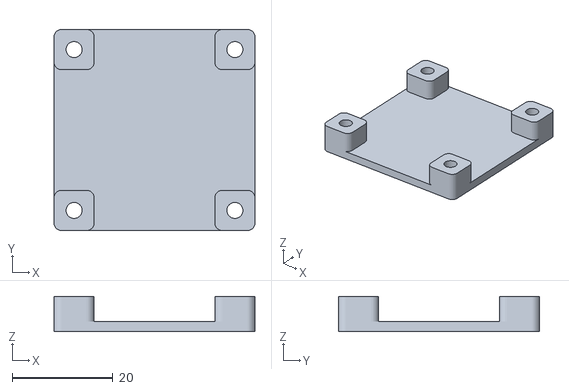
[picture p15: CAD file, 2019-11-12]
case/40mm_fan_cover.stl
40.0 x 40.0 x 7.00

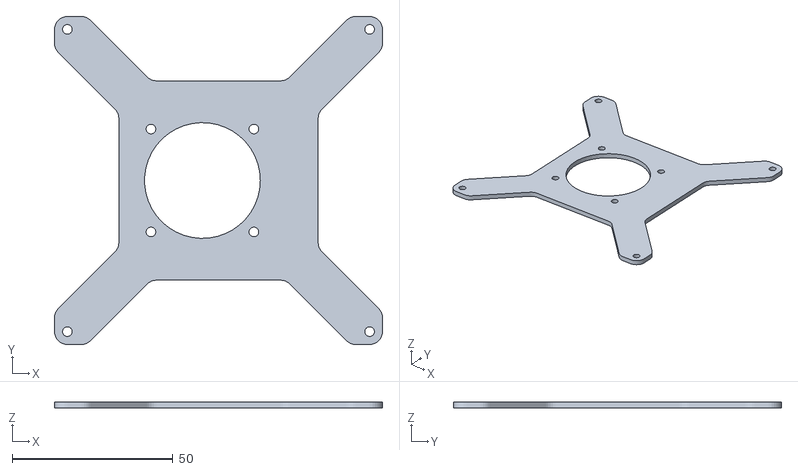
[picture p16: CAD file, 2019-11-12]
case/ESPE_basic_top_40mm.stl
102.0 x 102.0 x 2.00

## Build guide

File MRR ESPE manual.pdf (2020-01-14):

1

# MRR ESPE

# Version 0.5

# Getting Started

Document version: 1.1
Document date: January 14, 2020

Copyright 2020 Maple Rain Research Co., Ltd.

2

## Contents

3

4

### Features

The MRR ESPE is a 32-bit 3D printer control board using an ESP32 microcontroller. Besides interpreting G-codes for 3D printing, the ESP32 microcontroller acts as a web server that provides a web interface for controlling the printer. The board comes with the following features: - Able to use up to 5 stepper drivers—X, Y, Z, E0, and E1—and also allowing up to 2

motors to be connected in parallel for Z axis, with support to easily configure use of Trinamic SPI stepper drivers using jumpers - 12V to 24V input power supply

- Allows separate power supply to be used for the heated bed through use of an optocoupler - X, Y, and Z min endstops - Allows the use of a Z-axis probe, such as an inductive sensor, running on the input

supply voltage (12V to 24V) - Firmware controllable fans (part cooling fan; heat sink cooling fan; case fan; and one

extra fan) - AUX1 connector for use with an external host, such as the closed-source MKS TFT32

- LCD connector for use with an LCD controller such as that found on Creality 3D printers - Web interface over 802.11 b/g/n Wi-Fi (implemented via firmware) - I2S stepper stream with 10 additional I2S output pins

Specifications (ESP32 microcontroller) - Tensilica Xtensa 32-bit LX6 microprocessor with dual cores - Clock frequency up to 240 MHz

- 802.11 b/g/n Wi-Fi supporting WFA, WPA/WPA2 and WAPI - Bluetooth v4.2 BR/EDR and Bluetooth Low Energy (BLE) - ROM: 448 KB
- SRAM: 520 KB
- Flash memory: 4 MB
- Peripheral input/output: ADC, DAC, I²C, UART, CAN 2.0, SPI, I²S, RMII, PWM, and more.

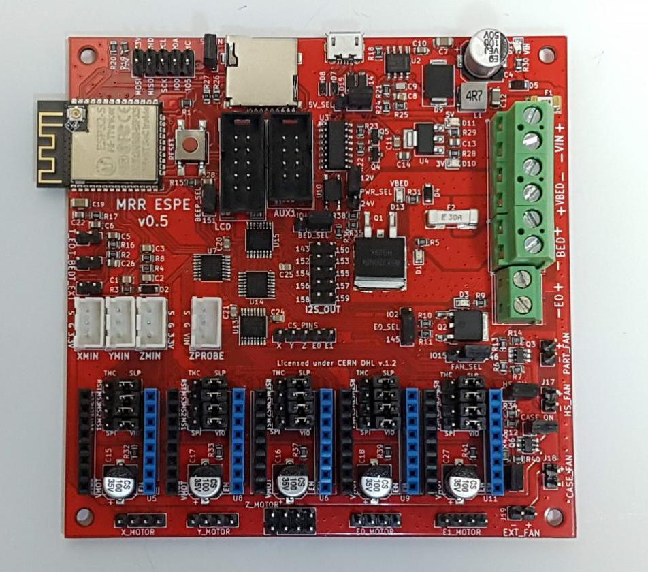
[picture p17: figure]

5

### Board Layout

Physical dimensions - 102 mm by 102 mm

- M3 mounting holes at each corner. Center of mounting hole is 4 mm from the edges of the board. - Board thickness: 1.6 mm

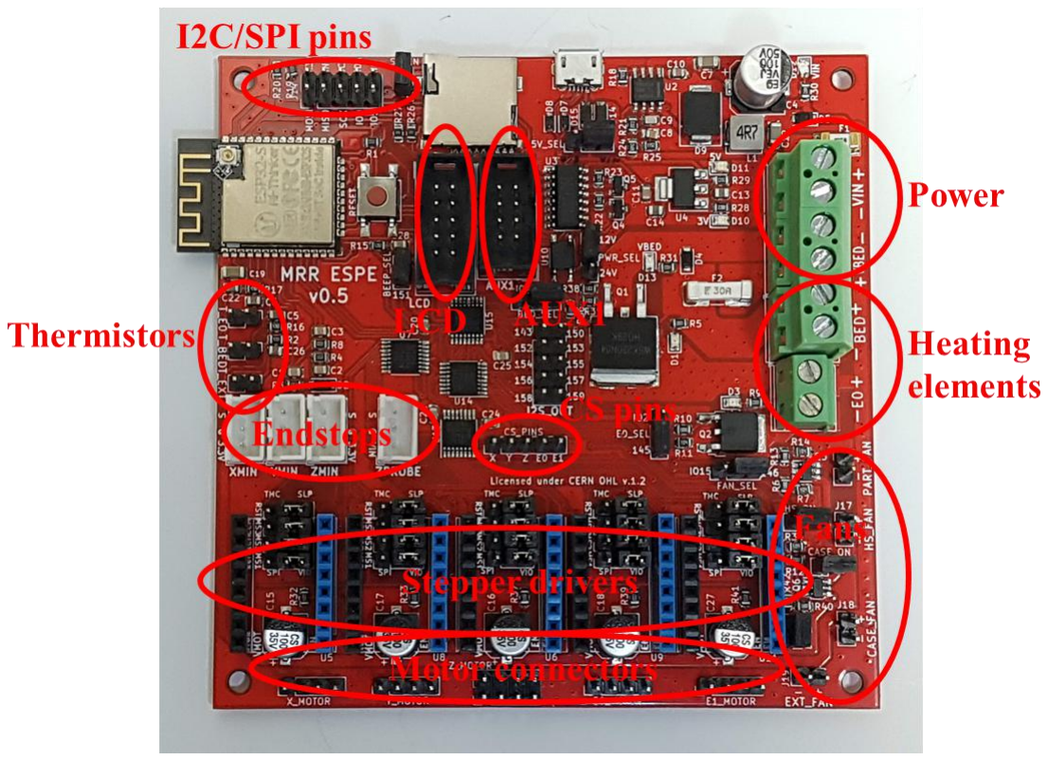
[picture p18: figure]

6

### Connectors

Power
VIN:- Main power supply for the MRR ESPE. - Accepts supply voltage from 12V to 24V. - Used to power all devices connected to the MRR ESPE, except the heated bed. This

includes the hot end heating block, motors, and fans. - Maximum current allowed is 10A. VBED: - Power supply for the heated bed. - Accepts supply voltage from 12V to 24V. - Maximum current allowed is 15A. Heating elements

BED: - For connecting to a heated bed. - Maximum current allowed is 15A.

7

E0: - For connecting to the hot end heating block. - Maximum current allowed is 5A. Fans

PART_FAN: - Connector for part cooling fan. - Use a fan rated for a voltage that matches the voltage of VIN. - Can be controlled by firmware. HS_FAN: - Connector for hot end’s heatsink cooling fan. - Use a fan rated for a voltage that matches the voltage of VIN. - Can be controlled via firmware; use the HS_ON jumper to set it always on. CASE_FAN: - Connector for case fan. - Use a fan rated for a voltage that matches the voltage of VIN. - Can be controlled via firmware; use the CASE_ON jumper to set it always on. EXT_FAN: - Connector for extra fan. - Use a fan rated for a voltage that matches the voltage of VIN. - Can be controlled via firmware; use the EXT_ON jumper to set it always on. Thermistors

T_BED: - Thermistor for heated bed. T_E0: - Thermistor for hot end. T_E1: - Extra thermistor; can be used for enclosure thermistor. Endstops

X_MIN: - X minimum endstop. - Externally pulled high to 3.3V. Y_MIN: - Y minimum endstop. - Externally pulled high to 3.3V.

8

Z_MIN: - Z minimum endstop. - Externally pulled high to 3.3V. ZPROBE: - For connecting to a capacitive or inductive probe instead of a mechanical switch for

the Z minimum endstop. - The probe will be supplied with the same voltage as VIN. Please make sure that the

connected probe is rated for this voltage. Stepper drivers - There are five sets of connectors for five stepper drivers. - Note the orientation of the stepper driver. The EN pin on the stepper driver should be

in the row toward the fan connectors. Motors

X_MOTOR: - For connecting to the X-axis stepper motor. Y_MOTOR: - For connecting to the Y-axis stepper motor. Z_MOTOR: - For connecting to the Z-axis stepper motor. E0_MOTOR: - For connecting to the extruder stepper motor. E1_MOTOR: - For connecting to an addition stepper motor, which can be a second extruder, or a

second stepper motor for the Z axis. Others

AUX1: - For connecting to an external host controller like the MKS TFT32 using UART. - Supply voltage on this connector is 5V. LCD: - For connecting to a LCD controller like those used on Creality 3D printers. - Supply voltage on this connector is 5V. I2C/SPI:

9

- Breakout headers for I2C and SPI pins. - GPIO 0 (IO0) is also available for troubleshooting purposes. Connect GPIO 0 to

ground, then boot/reset the board to manually enter flash mode. USB: - For connecting to an external host computer. - When connected to a host computer, a serial terminal can be used to send gcodes to

the MRR ESPE. MicroSD: - For use with a microSD card. - The microcontroller can work with partitions up to 4 GB in size. - There is no automatic detection of microSD card. Each time a card is inserted, the

MRR ESPE needs to be informed via the gcode M21.

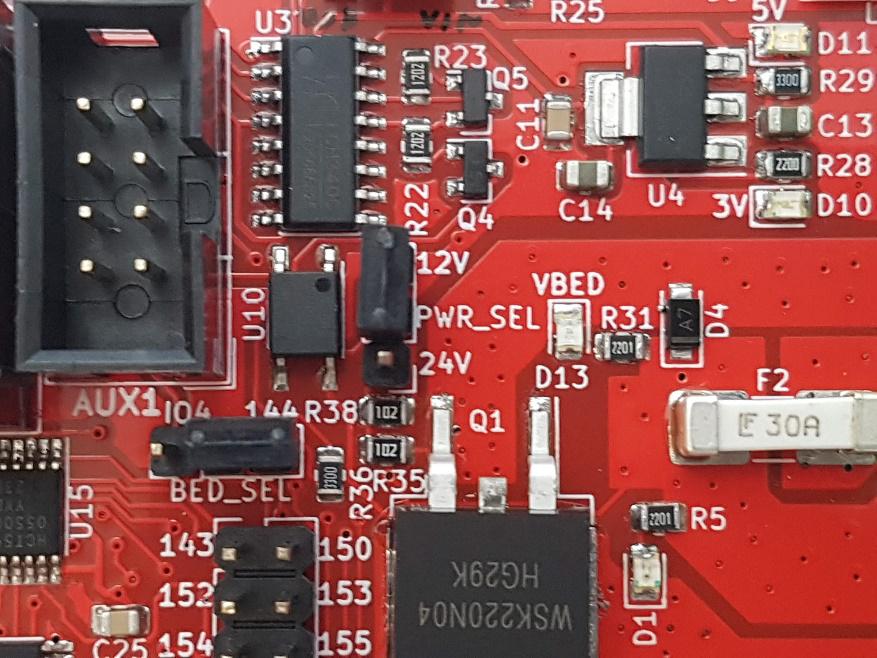
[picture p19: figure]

10

### Jumpers

USB power
5V_SEL: - Allows the board to be powered via USB or VIN. - This jumper should usually be connected to VIN. - Connect this jumper to VUSB only when flashing the firmware, or when you need to

power the board via USB. Note: Powering the board via USB while heating the heated bed can cause unstable operation. Bed MOSFET signal voltage

PWR_SEL: - Allows the bed MOSFET’s gate to be powered by a higher voltage so as to reduce

RDS(on). - When powered using 12V to 18V for VBED, set the jumper to connect the middle pin

with the pin labeled “12V”. - When powered by a voltage above 18V for VBED, set the jumper to connect the

middle pin with the pin labeled “24V”.

Stepper motor drivers
MS1: - Connect to VIO to set MS1 to high for microstepping; connect to SPI side to enable

SPI mode for Trinamic drivers. MS2:

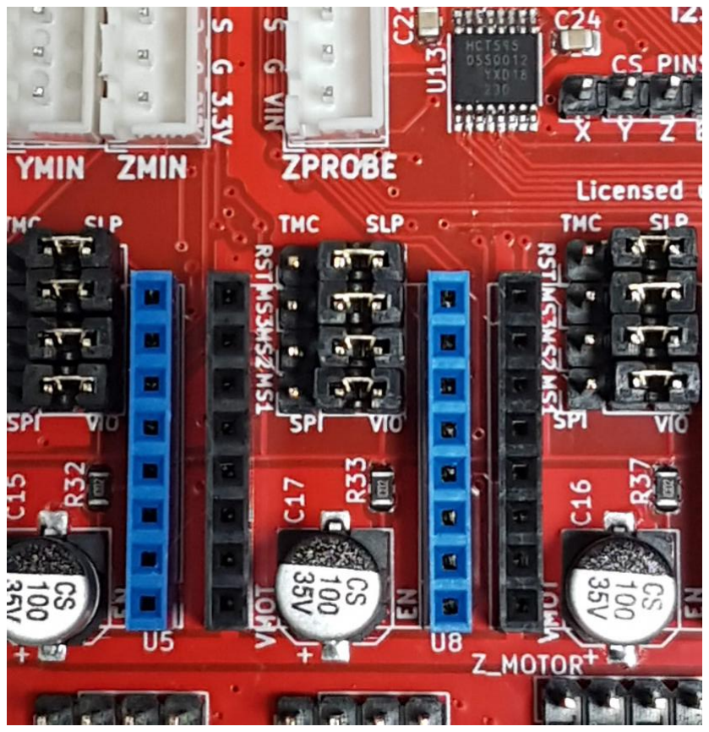
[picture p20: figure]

11

- Connect to VIO to set MS2 to high for microstepping; connect to SPI side to enable SPI mode for Trinamic drivers. MS3: - Connect to VIO to set MS3 to high for microstepping; connect to SPI side to enable

SPI mode for Trinamic drivers. RST:- Connect to SLP if using A4988 or DRV8825 drivers, or if using Trinamic drivers in

standalone mode; connect to SPI side to enable SPI mode for Trinamic drivers.

Fans
HS_ON: - Connect (close) to keep the heat sink fan always on. - Leave open to allow the firmware to control the heat sink fan. CASE_ON: - Connect (close) to keep the case fan always on. - Leave open to allow the firmware to control the case fan. EXT_ON: - Connect (close) to keep the extra fan always on. - Leave open to allow the firmware to control the extra fan.

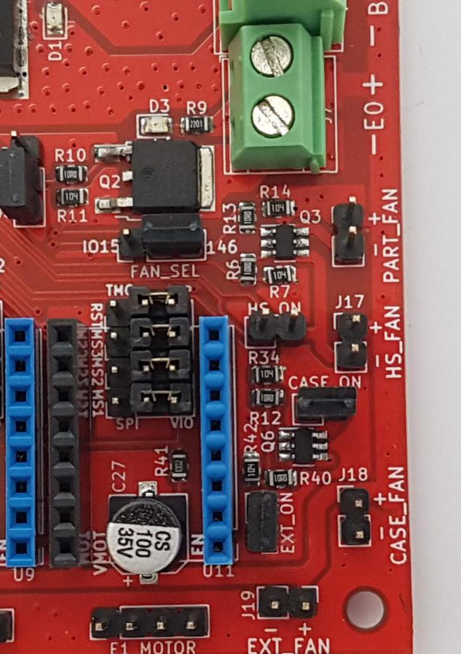
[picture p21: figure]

12

PWM signal
BED_SEL: - Connect BED_SEL pin to either IO2 (native ESP32 pin) or 145 (I2S pin). E0_SEL: - Connect E0_SEL pin to either IO5 (native ESP32 pin) or 144 (I2S pin). FAN_SEL: - Connect FAN_SEL pin to either IO15 (native ESP32 pin) or 146 (I2S pin).

13

### Connecting the board

Endstops: - Connect the cables for the X, Y, and Z minimum endstops to the board’s XMIN, YMIN, and ZMIN respectively. - Note the polarity: V for 3.3V, G for ground, and S for signal. Probe: - If using a Z probe, such as an inductive probe, connect the probe’s cable to ZPROBE

instead of ZMIN. - Note the polarity: V for 12V to 24V (depends on VIN voltage), G for ground, and S

for signal. Connecting the probe wrongly may damage the probe. Thermistors: - Connect the hotend thermistor to T_E0. - If using a heated bed, connect the heated bed thermistor to T_BED. - An additional thermistor (such as for enclosure temperature) can be connected to

T_E1. Stepper drivers and motors: - Set the jumpers for each stepper driver to the required microstepping (if using A4988, DRV8825, or Trinamic steppers in standalone mode) or to the SPI side (if using

Trinamic steppers in SPI mode). - Place the stepper drivers for each motor (X, Y, Z, E0, and E1) into the set of

connectors corresponding to their motor connectors. - Note the orientation of the stepper driver. The EN pin on the stepper driver should be

in the row toward the fan connectors. Placing the stepper driver in the wrong orientation can damage the stepper driver. - Connect the cables from the X, Y, Z, and extruder motors to X_MOTOR, Y_MOTOR, Z_MOTOR, and E0_MOTOR on the board respectively. An additional motor can be

connected to E1_MOTOR if used. - For Z axis, 2 motors can be connected in parallel. Fans:- Connect the case fan (for cooling the control board) to CASE_FAN. Leave

CASE_ON jumper open to control this fan via firmware; close (short) CASE_ON

14

jumper to make this fan always on. - Connect the hotend heatsink cooling fan (for cooling the heat sink on the hot end) to

HS_FAN. Leave HS_ON jumper open to control this fan via firmware; close (short) HS_ON jumper to make this fan always on. - Connect the part cooling fan (controlled by gcode) to PART_FAN. Set the FAN_SEL

jumper to either IO15 (use native pins) or 146 (use I2S). - An extra fan can be connected to EXT_FAN. Leave EXT_ON jumper open to control

this fan via firmware; close (short) EXT_ON jumper to make this fan always on. - Note the polarity; usually, the red or yellow wire is positive (+), and the black or blue

wire is negative (-). Reversing polarity may damage the fan. Hotend: - Connect the cable for the hotend’s heating cartridge to E0. - Polarity matters if you are connecting this to an external MOSFET. - Set the E0_SEL jumper to either IO2 (use native pins) or 145 (use I2S). Heated bed: - If using a heated bed, connect the cable for the heated bed to BED. - Polarity matters if you are connecting this to an external MOSFET. - Set the BED_SEL jumper to either IO4 (use native pins) or 144 (use I2S). Main power supply: - Connect the board’s power supply (12V to 24V) to VIN. - Note the polarity; the positive wire (usually red) should go to +, while the ground

wire (usually black) goes to -. Reversing polarity can damage the board and render it unusable. It may also damage the hotend MOSFET, causing the hotend to heat up uncontrollably when power is turned on. This may become a potential fire hazard. Heated bed power supply: - Connect the power supply for the heated bed (12V to 24V) to VBED. A separate

power supply from VIN can be used as the heated bed is controlled via an optocoupler. - Note the polarity; the positive wire (usually red) should go to +, while the ground

wire (usually black) goes to -. Reversing polarity can damage the board and cause

15

the bed to heat up uncontrollably when power is turned on. This may become a potential fire hazard. - Set the PWR_SEL jumper according to the voltage being used for VBED: when using

12V to 18V for VBED, set the jumper to connect the middle pin with the pin labeled “12V”; when using a voltage above 18V for VBED, set the jumper to connect the middle pin with the pin labeled “24V”. LCD controller: - A LCD controller, such as those used on Creality 3D printers, can be connected to

LCD. - Close (short) BEEP_SEL to enable the beeper on the LCD controller; leave

BEEP_SEL open if you do not want the beeper to sound. MicroSD card: - Insert a microSD card into the microSD card slot. - Close (short) SD_EN jumper to use the microSD card on the board. Leave SD_EN

jumper open to use an external SD card reader; the CS_SEL of this external card reader needs to be connected to IO5 on the breakout pins. External host: - An external host controller, such as the MKS TFT32, can be connected to AUX1.

16

### Setting Up the Firmware

The board is sold without the firmware being flashed. Therefore, when using it for the first time, the firmware must be configured and flashed. Flashing firmware

- Download | a | copy | of | the | firmware, | such | as | from
https://github.com/maplerainresearch/Marlin or the main Marlin repository at https://github.com/MarlinFirmware/Marlin.If this is downloaded as a ZIP file, it will need to be uncompressed to a directory on your local hard drive. - Connect the board via USB to your computer. Remember to set the 5V_SEL jumper

to VUSB so that the board gets powered through USB. If your computer does not detect the board, you may need to install drivers to support CH340 on your operating system. - Windows: http://www.wch.cn/download/CH341SER_EXE.html - Mac: http://www.wch.cn/downloads/CH341SER_MAC_ZIP.html - Linux (should already come with the OS):

http://www.wch.cn/downloads/CH341SER_LINUX_ZIP.html - If using Marlin, refer to the instructions at http://marlinfw.org/docs/basics/install.html

for the basics on configuring, building, and uploading Marlin firmware. Here, we will use Arduino IDE to build and upload the firmware. (Note: It is highly recommended to compile Marlin firmware using PlatformIO on VSCode. The specific instructions can be found here http://marlinfw.org/docs/basics/install_platformio_vscode.html.) - First, you need Arduino IDE installed on your computer (Windows, Mac, or

Linux). Go to Arduino IDE's download page (https://www.arduino.cc/en/main/software) to download the version of the IDE for your computer. Arduino IDE's installation guide can be found here. (https://www.arduino.cc/en/Guide/HomePage) - Once Arduino IDE has been installed, follow the instructions here to install the

ESP32 core for Arduino IDE. It is recommended to install the stable release. - Launch Arduino IDE, and open the sketch for the firmware. This file is named

Marlin.ino and can be found in the downloaded firmware's Marlin subdirectory. - In the IDE's menu, go to “Tools”, then “Board”, and choose “ESP32 Dev

Module” which is the generic ESP32 module. Then, under “Tools”, “Port”, choose the COM port that your board is connected to. For upload speed, go to

“Tools”, “Upload speed”, and set to “115200”. - Edit the Configuration.h and Configuration_adv.h files to define

17

the size of your printer, endstops, and other settings. See the section below for some basic settings which need to be changed. - Click on the “Upload” icon of the IDE to compile the firmware and flash it

onto the board. This will take quite a while. - Once the firmware has been flashed onto the board, you can open the IDE's

serial monitor (by pressing Ctrl+Shift+M, or from the menu via Tools, then Serial monitor) to make sure the firmware has been flashed properly. Enter M503 into the serial monitor and you should get a response from the board giving the current settings such as steps/mm and PID values. - Via the serial monitor, you can configure your WiFi settings. See the section

below on how to do so. You can also set up WiFi using a web browser (see relevant section below). - When uploading firmware for the first time, the board needs to be connected via USB

to the computer. Once over-the-air (OTA) update has been enabled, future uploads of firmware to the board can be carried out via WiFi. Setting up WiFi (via Terminal)

Once the firmware has been flashed for the first time, there is a need to do an initial setup for the WiFi settings. In Arduino IDE, open up the serial monitor to connect to the board. You can also use any other terminal program to open the COM port that the board is connected to. Then, type in the following commands 1, 2, and 5 to set up the board in station mode

(connect to an existing WiFi router). To set up in AP mode, use commands 3, 4, and 5. 1. [ESP100]abcd

## [ESP101]12345

WiFi settings; the above will connect to a SSID of abcd with password 12345. Change abcd and 12345. 2. [ESP103]STA

This will start up WiFi in station mode. The IP address of the webserver will be displayed in the terminal. Use this IP address to connect to the webserver. 3. [ESP105]abcd

## [ESP106]12345

WiFi settings; the above will create an access point with SSID of ESP32 and password 12345. WPA2 security will be used by default.

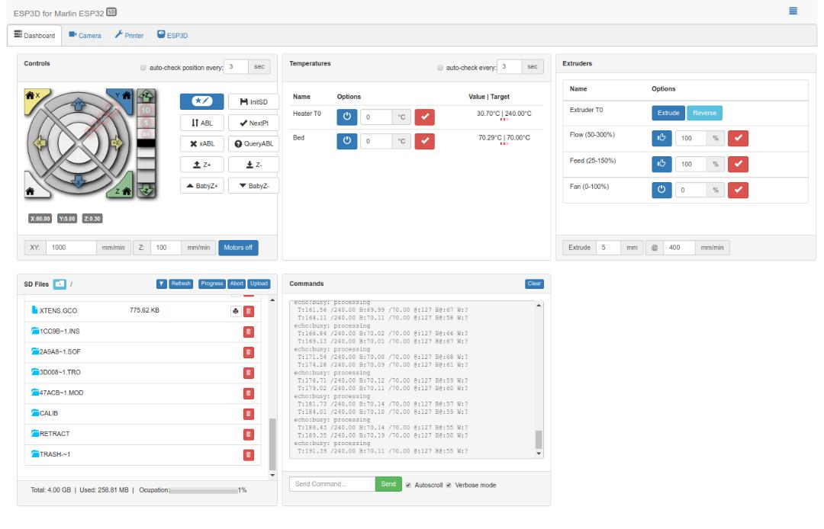
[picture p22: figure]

18

## 4. [ESP103]AP

This will start up WiFi in AP mode. 5. [ESP110]ON

This will turn on WiFi. Setting up WiFi (via WiFi)

When WiFi is not configured, the board will automatically become an access point (AP). The SSID of this AP is MARLIN_ESP and the default password is 12345678. Connect your computer to this AP, then open a web browser and go to the address 192.168.0.1 to open up a web interface to configure WiFi settings. For login credentials, use the user name admin and the default password admin to change the settings. Uploading the web UI - When you first go to the web UI address (if you have mDNS, this should be

http://marlinesp.local/ by default), you will be asked to upload the web UI files. Click on "Choose files", select index.html.gz, then upload. Then, refresh your browser page; the webUI should load. A copy of index.html.gz can be found in the firmware directory, under <firmware directory>/Marlin/data/. - If you have the Arduino ESP32 filesystem uploader, you can also choose to upload the

required files from Arduino IDE. After flashing the firmware, go to Tools, then choose ESP32 Sketch Data Upload.

19

Adding macros
The webUI (based on ESP3D) allows user-defined macros to be created. This allows “buttons” for custom commands (GCODE), such as buttons for babystepping, to be added to

the webUI. For example, to add a command to move to babystep Z by 0.01 downwards:

1. Create a text file with the gcode. In this case the gcode would be “M290 Z-0.01”. Save it with a “.g” extension. In this case, it can be named babyzdn.g. 2. Upload that file to the ESP3D File System (not to the SD card); this is the SPIFFS file

system, where index.html.gz is stored. 3. Click on the macro editor button in the controls panel. click the plus icon to add a

macro. Give it a name, select a color, set the target as ESP and enter the path to the gcode file you uploaded. 4. Click Save. Some ready-made macros can be found at:

https://github.com/maplerainresearch/MRR_ESPA/tree/master/firmware/macros

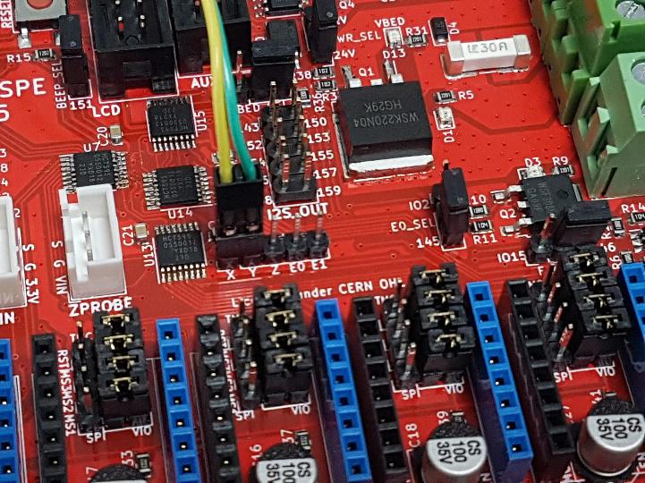
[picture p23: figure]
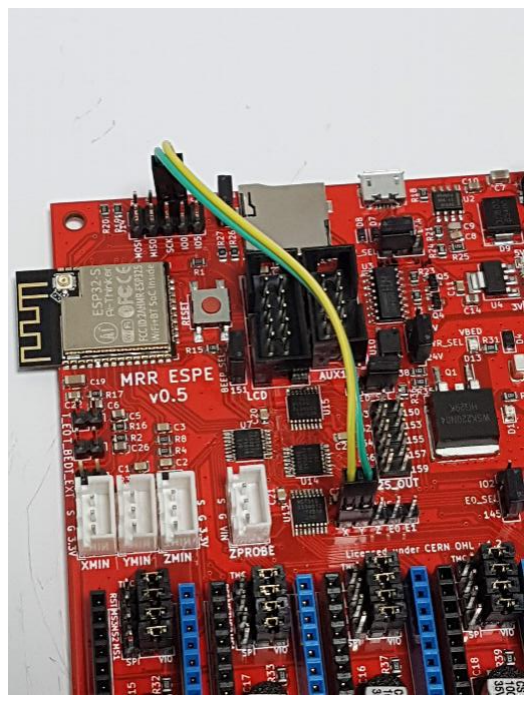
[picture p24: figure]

20

### Additional Notes

Wi-Fi performance
- Avoid placing the MRR ESPE within a metal case as it may adversely affect Wi-Fi performance. If necessary, expose the PCB antenna outside the case. Connecting Trinamic stepper motor drivers (SPI mode) - Jumpers are available to allow Trinamic stepper motor drivers using SPI mode to be

easily configured. By setting the jumpers correctly, the only wiring needed for each driver is a wire for the CS pin. - To configure a driver for SPI mode, connect the jumpers MS1, MS2, MS3, and RST

for that respective driver to the TMC side.

- Use a jumper wire to connect the respective CS_PIN (either X, Y, Z, E0, or E1) to an unused pin (IO0, IO4, IO2, IO15, SDA, or SCL).

21

Using 12V for heated bed
- When using 12V for the heated bed, the current drawn by the heated bed can be in excess of 10A. This can cause the board to become very hot; do not touch the board during operation. (Warning: Parts of the board, such as the VBED fuse, can reach temperatures above 100 degrees Celsius when heating the heated bed. Also, due to the high currents involved, wires use for the heated bed, including wires being used to connect to the PSU, may get very hot.) - It is highly recommended to have another fan to cool the underside of the board. This

fan can be connected in parallel with the case fan. It is also recommended to place a small heat sink on the heated bed MOSFET (Q1). Using GPIO0 (IO0)

On the ESP32, GPIO0 has a special function: it is pulled to GND when booting to enter flash mode. Therefore, it is not recommended to use this pin for functions which require it to be physically pulled to GND, as it will affect the booting up of the board. On the other hand, if you are facing problems trying to flash the board via USB, you can

connect GPIO0 to GND, then reset the board to enter flash mode.

22

### Troubleshooting

A common cause of issues with the board is a loose connection. Check to make sure all cables are firmly connected. Reverse polarity can also damage the board, so check that all cables are connected with correct polarity. - Issue: The endstops are not triggering. Check the endstops are connected correctly, especially the V, G, and S wires. Mechanical endstops usually only require two wires: ground (connect to G) and the

signal line (connect to S). - Issue: The motors do not move. Make sure the jumpers under the stepper drivers are connected correctly. For A4988

or DRV8825 drivers, the RST jumper must be connected to the SLP side. The other jumpers (MS1, MS2, MS3) can be connected to VIO to pull them high (to set microstepping), or left unconnected. - Issue: The heated bed does not heat up. The heated bed is powered via VBED, so make sure there is a power supply

connected to VBED. - Issue: The motors keep stopping during the print. Make sure the stepper drivers are adequately cooled. A case fan should be used to cool

the stepper drivers; this fan is connected to CASE_FAN. - Issue: The motor is turning the wrong way. You can either reverse the cable connection on the board, or edit the firmware’s

configuration to reverse the direction of the motor. - Issue: Files uploaded to the microSD card using the webUI are corrupted or partially

truncated. Disable #define MONITOR_DRIVER_STATUS in Configuration_adv.h by

commenting it out (adding double backslashes in front of it).

23

### Warnings

- This product uses high currents which may cause fires. Use with caution. - Do not use input voltages higher than 24V. Input current must not exceed 15A. - Do not attempt to use more than 15A for the heated bed. While the MOSFET is

capable of such currents, the connectors are not. If you need more than 15A, use an external MOSFET. In any case, it is highly recommended to use an external MOSFET for the heated bed to avoid drawing high currents through this product. - Do not attempt to use more than 5A for the hot end. While the MOSFET is capable of

such currents, the connectors are not. If you need more than 5A, use an external MOSFET. - Do not reverse polarity. - The breakout and endstop pins are rated for 3.3V, which is the voltage the ESP32

operates at. Attempting to feed inputs above 3.3V to these pins may damage the board. - It is recommended to power the board only via USB (i.e. turn off PSU power supply)

when flashing the board. Disclaimer

This product is provided as-is. While care has been taken to design a safe product, it is the user's responsibility to make sure precautions are taken to prevent damage or injury when using this product. This includes adhering to all warnings provided. By using this product, the user accepts responsibility to bear all liabilities from any damage or injury arising from the use of this product. License

Released under CERN Open Hardware Licence v1.2.

24

### Additional Information

Common Marlin settings
Below are some common settings in Marlin firmware which should be set to reflect your machine setup. This is not a comprehensive nor exhaustive list; the user is recommended to

## go through each setting in Configuration.h and Configuration_adv.h to make

sure all settings are correct. Note: Enabling a feature/setting means to uncomment it, i.e. make sure there is no // (double

slashes) in front of the #define statement. Configuration.h

#define MOTHERBOARD

This value defines which board is being used. It should be set to #define MOTHERBOARD BOARD_MRR_ESPE for the MRR ESPE. #define BAUDRATE

This is the speed used for serial communications. It should be set to #define BAUDRATE 115200 for the MRR ESPE. #define TEMP_HYSTERESIS

#define TEMP_BED_HYSTERESIS

These values define what is considered “close enough” when trying to reach a certain temperature for the hotend or heated bed. Due to the ADC of the ESP32, they should be set to a value of 5. #define PIDTEMPBED

This allows PID bed heating, and should be enabled. #define THERMAL_PROTECTION_HOTENDS

#define THERMAL_PROTECTION_BED

#define THERMAL_PROTECTION_CHAMBER

These settings enable safeguards against a broken or disconnected thermistor wire, and must be enabled. #define X_DRIVER_TYPE

25

#define Y_DRIVER_TYPE

#define Z_DRIVER_TYPE

#define E0_DRIVER_TYPE

Change the values of these to reflect the stepper driver being used for each axis. The default value is A4988. #define INVERT_X_DIR

#define INVERT_Y_DIR

#define INVERT_Z_DIR

#define INVERT_E0_DIR

Toggle these values between true and false to switch the direction of the stepper motors. #define X_HOME_DIR

#define Y_HOME_DIR

#define Z_HOME_DIR

The values of these should be -1 to use the minimum endstops. #define X_BED_SIZE

#define Y_BED_SIZE

#define Z_MAX_POS

These values should be set to the maximum sizes for your X, Y, and Z axes respectively. #define X_MIN_POS

#define Y_MIN_POS

These values reflect the position of the nozzle when the respective X and Y minimum endstops are triggered. Set to values of 0 if the endstops are triggered at the edges of the print area. Set to negative values if the endstops are triggered with the nozzle outside the print area. #define Z_MIN_POS

This value reflects the position of the nozzle when the Z minimum endstop is triggered. Set to 0 if the endstop are triggered at same height as the bed, or if using an autolevel probe. Set to a negative values if the endstop is triggered with the nozzle below the bed. #define Z_SAFE_HOMING

Enable this if you are using an autolevel probe and want to home the Z axis using the center

26

of the bed instead of at the edge (where the probe may fail to detect the bed). #define SDSUPPORT

This must be enabled to allow use of the onboard microSD card. #define SPI_SPEED SPI_HALF_SPEED

Enable this if you have “volume init” errors. Configuration_adv.h

#define TX_BUFFER_SIZE

Set to 128 for optimal speed. #define RX_BUFFER_SIZE

Set this to at least 1024. #define X_CS_PIN -1

#define Y_CS_PIN -1

#define Z_CS_PIN -1

#define E0_CS_PIN -1

#define E1_CS_PIN -1

If using Trinamic stepper drivers in SPI mode, uncomment the respective line for the axis, and change the -1 to the pin being used for CS (such as 21 or 22). #define ESP3D_WIFISUPPORT

#define WEBSUPPORT

#define OTASUPPORT

#define WIFI_CUSTOM_COMMAND

Enable this to allow the MRR ESPA to communicate via WiFi using the ESP3D webUI, and allow over-the-air (OTA) updates. Pins
Function | Marlin name | Pin
| Endstops
X min endstop | X_MIN_PIN | 35

27

Y min endstop | Y_MIN_PIN | 32
Z min endstop | Z_MIN_PIN | 33
I2S stream
I2S word select clock | I2S_WS | 26
I2S bit clock | I2S_BCK | 25
I2S data | I2S_DATA | 27
Stepper drivers
X step | X_STEP_PIN | 129
X direction | X_DIR_PIN | 130
X motor enable | X_ENABLE_PIN | 128
Y step | Y_STEP_PIN | 132
Y direction | Y_DIR_PIN | 133
Y motor enable | Y_ENABLE_PIN | 131
Z step | Z_STEP_PIN | 135
Z direction | Z_DIR_PIN | 136
Z motor enable | Z_ENABLE_PIN | 134
E0 step | E0_STEP_PIN | 138
E0 direction | E0_DIR_PIN | 139
E0 motor enable | E0_ENABLE_PIN | 137
E1 step | E1_STEP_PIN | 141
E1 direction | E1_DIR_PIN | 142
E1 motor enable | E1_ENABLE_PIN | 140
Thermistors
Hotend thermistor | TEMP_0_PIN | 36
Heated bed thermistor | TEMP_BED_PIN | 39
Extra thermistor | TEMP_1_PIN | 34
Heating elements
Hotend MOSFET gate | HEATER_0_PIN | 2 or 145
Heated bed MOSFET gate | HEATER_BED_PIN | 4 or 144
Fan
Part cooling fan | FAN_PIN | 15 or 146
Case fan | CONTROLLER_FAN_PIN | 147
Heat sink fan | E0_AUTO_FAN_PIN | 148
Extra fan | FAN1_PIN | 149

28

MicroSD card
SD card select | SDSS (or SS_PIN) | 5
| SPI pins
MOSI | MOSI_PIN | 23
MISO | MISO_PIN | 19
SCK | SCK_PIN | 18
LCD controller
LCD_RS | LCD_PINS_RS | 13
LCD_EN | LCD_PINS_ENABLE | 17
LCD_D4 | LCD_PINS_D4 | 16
Beeper | BEEPER_PIN | 151
BTN_EN1 | BTN_EN1 | 0
BTN_EN2 | BTN_EN2 | 12
BTN_ENC | BTN_ENC | 14
I2C pins
SDA | SDA (not used) | 21
SCL | SCL (not used) | 22
Others
I2S output 143 | (not used) | 143
I2S output 150 | (not used) | 150
I2S output 152 | (not used) | 152
I2S output 153 | (not used) | 153
I2S output 154 | (not used) | 154
I2S output 155 | (not used) | 155
I2S output 156 | (not used) | 156
I2S output 157 | (not used) | 157
I2S output 158 | (not used) | 158
I2S output 159 | (not used) | 159

29

Document Revision History
November 1, 2019
- Document created. January 14, 2020
- Updated with new ESP3D commands and configuration requirements due to ESP3DLib integration into Marlin. - Added note about issue with MONITOR_DRIVER_STATUS causing problems with

SD file uploads.

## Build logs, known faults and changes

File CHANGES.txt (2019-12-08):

Changes
-------
v0.5rev1
--------
- Fixed TX and RX on AUX1 connector (issue with v0.5).

v0.5
----
- Changed 74HCT595 footprint to TSSOP for better use of PCB space.
- Added PWR_SEL jumper to select between 12V and 24V for heated bed MOSFET gate.
- Added debounce capacitor to RESET button.
- Change VUSB_EN jumper to 5V_SEL jumper, to select between VUSB and VIN for 5V source.
- Note: The RX and TX pins labeled on the board are wrongly connected (RX is connected to UART+ and TX to UART-. This prevents the AUX1 connector from working with controllers like the MKS TFT32 unless dupont connectors are used to connect each pin separately.

v0.4
----
- Test version.
- 4 x 74HCT595 (32 outputs, TTL version running at VCC=5V):
  - 5 x stepper drivers (5 x 3 outputs = 15 outputs from lower 16 pins).
  - 74HCT595 for fan controls (3 outputs from upper 16 pins):
    - CONTROLLER_FAN, E0_AUTO_FAN, E1_AUTO_FAN
  - Jumpers to select between ESP32 and I2S pins (4 outputs from upper 16 pins):
    - Bed MOSFET
    - E0 MOSFET
    - Part-cooling fan
    - Beeper
  - Unused pin connector (10-pin).
- 2 x WST3392 for fan PWM control:
  - Part-cooling fan
  - CONTROLLER_FAN, E0_AUTO_FAN, E1_AUTO_FAN + jumpers for "always on" operation
- Total board layout revamp to allow 5 stepper drivers, with board size 102mm x 102mm.
- Changed power MOSFETs
  - WSK220N04 for Bed MOSFET.
  - WSF3085 for E0 MOSFET.
- Added T_EXT connector (IO34) for extra thermistor.
- Added VUSB_EN jumper to disable VUSB power.
- Added SD_EN jumper to select between onboard microSD card or external card.

v0.3
----
- Test version; 4 x 74HC595 instead of 2 x 74HC595; some of the additional I2S pins are connected to male headers for use in testing.
- Added pull-up resistors to MOTOR_EN pins.
- Changed endstop and thermistor connectors to JST XH.
- Changed TPS54340-related layout to take into consideration recommended PCB layout in data sheet.
- Changed pins to allow better ground plane under I2S to reduce noise.

v0.2
----
- Widened trace width of VBED-related traces.
- Changed F2 to use a bigger (Littelfuse 0456 series) 30A fuse.

v0.1
----
- Initial version.
- Changes from MRR_ESPA v1.0
  - Added 74HC595 to drive stepper motors.
  - Reorganized board layout
    - microSD card slot mounted on reverse side to free up additional footprint on top side.
  - Changed F2 to a bigger 30A fuse.
- Support for Creality LCD.
- Jumpers for TMC2130 SPI mode support
  - Breakout pins for X_CS, Y_CS, Z_CS, and E_CS which can then be connected with jumper wires to available pins.

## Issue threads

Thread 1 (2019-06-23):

Feedback on MRR ESPE

vivian-ng, 2019-06-23:
A prototype of the MRR ESPE board, which uses 2 x 74HC595 shift registers to implement I2S stepper stream for the ESP32, is out. Most of the board design is based on the MRR ESPA board (many many lessons learnt there) while the I2S stepper stream is courtesy of simon-jouet.

I will be testing it with luc-github's Marlin fork (which comes with his ESP3D embedded) once he has managed to rebase his fork to incorporate the latest I2S-related updates from the main Marlin repo.

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

I can probably improve the use of the "real estate" more, and I probably should.

vivian-ng, 2019-06-27:
A quick update on this board.

Basic functionality has been checked, short of an actual test print. The motors can move, the heaters (heat bed and hot end) can work. Temperature readings seem to be fluctuating slightly, but nothing that will cause issues with prints, I think. The board also works with the Creality LCD controller. I have tried to connect a Reprap full graphics smart controller (aka LCD12864), and it works.

One thing to note: Linear Advance does not work with I2S. This probably has to do with how linear advance is implemented now. But it should not be an issue for those using direct drive extruders.

vivian-ng, 2019-08-02:
The next version of this board will add further functionality using 4x74HC595 shift registers. I will also be using the TTL version of the shift registers to see if it helps improve reliability. But the TTL version costs like 4 times more than the CMOS version... which drives up the BOM cost.

Preliminary testing has shown that the I2S output pins can be used for PWM output, which means it can be used to drive the various MOSFETs (heated bed, hot end, fans). This frees up pins on the ESP32, which potentially can then be used for the CS pins and UART pins for Trinamic drivers.

Stay tuned for 5 stepper drivers, multiple fan outputs, and 3 thermistors!

vivian-ng, 2019-08-13:
v0.3 of the board (will release files soon) has been tested to compile with TMC2130 support for Marlin 2.0 bugsfix. A native ESP32 pin needs to be used for the CS pin, though. For example, GPIO21 (SDA) or GPIO22 (SCL).

TMC2208 and TMC2209 drivers will need a bit more work, since they will likely need to use software serial, and there are currently issues with compiling software serial on TMCStepper library:
[ESP32 is no SoftwareSerial Compatible Platform](https://github.com/teemuatlut/TMCStepper/issues/59)
[ESP32 compatibility](https://github.com/teemuatlut/TMCStepper/issues/35)
Each of these drivers also needs 2 native ESP32 pins, which is a luxury that cannot be easily spared since the ESP32 has very few pins to start with in the first place. So it is unlikely the board will ever be designed to support TMC2208/TMC2209 drivers via jumper settings.

For SPI mode, users will just need one jumper wire (female-to-female) per stepper driver to connect the CS pin for the respective axis to a spare pin (GPIO21, and GPIO22; plus GPIO2, GPIO4, and GPIO15 when using I2S to drive the PWM for heated bed, hot end, and part fan).

vivian-ng, 2019-10-09:
Updates on this board, which uses I2S for the stepper stream as well as PWM.

1. PWM for heated bed, hotend, and fans have been tested to be working fine. No issues with printing.

2. Experiencing resets every time babystepping is attempted through LCD screen. I have not been able to determine if this is a software or hardware issue.

3. Similar to issue 2 above, there seems to be issues with manual mesh bed leveling via the LCD; every time I tried to do this, it will home, and then after moving to the first probe point, it will reboot. I think there two issues are linked, but I am not sure how.

4. Random resets in coreXY setup. The board runs fine on a cartesian printer. But when it is used for coreXY, it seems there is some instability in the stepper stream that triggers random resets. I think this is likely the DIR or EN pin value, because the random reset happens only when it is trying to switch direction, or switch axis.

vivian-ng, 2019-10-10:
Just for troubleshooting, as record, and also to see if there are any wise men around to help. This is the error when homing on a coreXY printer running on I2S stepper stream.
```
PC      : 0x400f418e  PS      : 0x00060931  A0      : 0x800f2abd  A1      : 0x3ffbe620  ␍␊
A2      : 0x00000000  A3      : 0x00000001  A4      : 0x3f000000  A5      : 0x00000000  ␍␊
A6      : 0x00000000  A7      : 0x3ffde474  A8      : 0x800f4188  A9      : 0x3ffc3080  ␍␊
A10     : 0x00000000  A11     : 0x3ffdea38  A12     : 0x4000bff0  A13     : 0x3ffbe7c0  ␍␊
A14     : 0x00002aaa  A15     : 0x00000000  SAR     : 0x00000020  EXCCAUSE: 0x00000004  ␍␊
EXCVADDR: 0x00000000  LBEG    : 0x40002390  LEND    : 0x4000239f  LCOUNT  : 0x00000000  ␍␊
Core 1 was running in ISR context:␍␊
EPC1    : 0x400f418e  EPC2    : 0x00000000  EPC3    : 0x00000000  EPC4    : 0x40082a51␍␊
Backtrace: 0x400f418e:0x3ffbe620 0x400f2aba:0x3ffbe700 0x400f15a6:0x3ffbe720 0x400f1613:0x3ffbe740 0x400f509f:0x3ffbe760 0x400f50bf:0x3ffbe780 0x40080fa5:0x3ffbe7a0 0x40081859:0x3ffbe7c0 0x4000bfed:0x3ffb1c40 0x40089d2d:0x3ffb1c50 0x4008babf:0x3ffb1c70 0x4008c144:0x3ffb1c90 0x40084a74:0x3ffb1cb0 0x40084aa9:0x3ffb1cd0 0x4008618d:0x3ffb1cf0 0x4000beaf:0x3ffb1d10 0x4016a7af:0x3ffb1d30 0x4016a781:0x3ffb1d50 0x400fac07:0x3ffb1d70 0x400ff61e:0x3ffb1db0 0x400e1056:0x3ffb1dd0 0x400e0cdd:0x3ffb1df0 0x400d311b:0x3ffb1e10 0x400e1358:0x3ffb1e30 0x400f2bae:0x3ffb1e50 0x400f1e77:0x3ffb1e70 0x400f1f3a:0x3ffb1ed0 0x400e3295:0x3ffb1f00 0x400e4b0b:0x3ffb1f30 0x400e52ad:0x3ffb1f50 0x400e695c:0x3ffb1f70 0x400e15c5:0x3ffb1f90 0x40107529:0x3ffb1fb0 0x400884a5:0x3ffb1fd0␍␊
```

The decoded stack:
```
PC: 0x400f418e: Stepper::endstop_triggered(AxisEnum) at Marlin/src/module/stepper.cpp line 2228
EXCVADDR: 0x00000000
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
vivian-ng, 2019-12-08:
@luc-github pointed out a mistake on the schematic/PCB of v0.5. The RX and TX pins are wrongly connected (they are swapped). On v0.5, that pin labeled TX is actually connected to UART- and the pin labeled RX is actually connected to UART+. This prevents the AUX1 connector from working with MKS TFT32 and other similar controllers using AUX1. To use such controllers, you will need to use dupont connectors.

I will put up a v0.5rev1 to fix this as soon as I can.

vivian-ng, 2019-12-13:
I have added a simple adapter board to fix the AUX1 issue, design can be found [here](https://github.com/maplerainresearch/MRR_ESPE/tree/master/adapters/AUX1_adapter).

Still untested. Waiting for JLCPCB to deliver the PCB. But it is a relatively simple design and I do not expect any problems.

vivian-ng, 2019-12-19:
The [adapter board to fix the AUX1 issue](https://github.com/maplerainresearch/MRR_ESPE/tree/master/adapters/AUX1_adapter) has been tested to work.

Another adapter board to break out the LCD connector pins to the EXP1 and EXP2 used in more common RepRapDiscount Full Graphics Smart Controllers can be found [here](https://github.com/maplerainresearch/MRR_ESPE/tree/master/adapters/LCD_adapter). To use with this controller, `Configuration.h` needs to be:
```
#define REPRAP_DISCOUNT_FULL_GRAPHIC_SMART_CONTROLLER
#define ST7920_DELAY_1 DELAY_NS(500)
#define ST7920_DELAY_2 DELAY_NS(500)
#define ST7920_DELAY_3 DELAY_NS(500)
```

The delays are needed for the display to work without being garbled.

Some more info can be found [here](https://teck78.blogspot.com/2019/12/the-lcd-connector-on-mrr-espe-which-is.html).

vivian-ng, 2020-01-14:
It seems that `#define MONITOR_DRIVER_STATUS` will affect the SD file uploads. Once I disabled this feature, all my uploads worked, even at full SPI speed. Tested on Ender-3 with MRR ESPE + TMC2130 drivers in SPI mode on X and Y axes (basically, my working test setup). Also tested on a bare MRR ESPA with TMC2130 drivers in SPI mode on X and Y.

Background:
I noticed that "Upload failed" was not being shown on my web serial terminal window on the webUI, but it was showing over a separate serial terminal window (over USB). At the same time, I was "X driver overtemperature warning!" and "Y driver overtemperature warning!" when the "Upload failed" message appears. Once I disabled `#define MONITOR_DRIVER_STATUS`, my uploads were fine, no warning messages, and the file sizes for consistent.

vivian-ng, 2020-01-16:
[PR#16581](https://github.com/MarlinFirmware/Marlin/pull/16581) sent to add sanity check that throws an error when TMC SPI drivers are in use with MONITOR_DRIVER_STATUS and SDSUPPORT both enabled. The user will then need to decide which to disable (most probably MONITOR_DRIVER_STATUS since SDSUPPORT is essential for sending files for print via the webUI).

vivian-ng, 2020-03-03:
The issue with babystepping and linear advance not working on I2S stepper stream has been given its own [issue](https://github.com/maplerainresearch/MRR_ESPE/issues/4).

wuxiaoyi88, 2020-04-21:
Today, using my own soldered ESPE PCB board, I did a firmware write, brush the marlin.2.02 version. Brush writing is normal, power test found that the BED heat transfer bed automatically heated.Not controlled, I do n’t know if the hardware is not welded well, or the hot bed cannot be controlled because of the firmware configuration problem. At present, there is no problem, but the stepper motor can walk normally, The E0 extrusion head can be heated normally.

vivian-ng, 2020-04-21:
@wuxiaoyi88
> Today, using my own soldered ESPE PCB board, I did a firmware write, brush the marlin.2.02 version. Brush writing is normal, power test found that the BED heat transfer bed automatically heated.Not controlled, I do n’t know if the hardware is not welded well, or the hot bed cannot be controlled because of the firmware configuration problem. At present, there is no problem, but the stepper motor can walk normally, The E0 extrusion head can be heated normally.

Please check your soldering. Maybe change your bed MOSFET, it could be broken. If need be, after your have done your own troubleshooting, post a separate issue with details of the problem.

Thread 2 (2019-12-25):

MRR ESPE with Trinamic drivers in UART mode

vivian-ng, 2019-12-25:
I received an email asking about TMC2209 drivers in UART mode. I thought it best to move the conversation to a more public space so that the collective wisdom of the open source community can be harnessed.

First, @luc-github has managed to use TMC2208 in standalone (aka "dumb") mode which does not use UART at all. Basically, the driver is configured using jumper pins much like normal "dumb" drivers like A4988.

For the MRR ESPE, the issues with getting UART mode working are:
1. **Native ESP32 pins**. Unlike the MRR ESPA, the MRR ESPE has more unused native pins since I2S is being used for stepper control and PWM. So by default, the MRR ESPE has 5 unused pins. If the LCD controller is not used, this frees another 6 pins for a total of 11 pins. Which means 5 axes (5 stepper drivers) can be supported as long as the serial ports for them can be configured.
2. **Hardware serial**. While the ESP32 has 3 sets of hardware serial, I have seen a lot of articles regarding getting all 3 to work. Most can get 2 sets working. One set will be used for serial terminal (USB to UART) already; that leaves only one other set of hardware serial for TMC driver in UART mode.
3. **Software serial**. The lack of hardware serial is usually overcome with software serial. But software serial support for ESP32 on the TMCStepper library is still being worked on. Unless someone is able to work on the software development for this, software serial will not be an option at all. But if someone manages to develop support for software serial on the ESP32 in the TMCStepper library, the MRR ESPE can theoretically use TMC drivers in UART mode (if the LCD controller is not used).

Consolidating:
- Trinamic drivers in standalone mode works.
- Trinamic drivers in SPI mode works. If you need silent operations, TMC2130 drivers can be used. For higher currents, TMC5160 should work too.
- Trinamic drivers (TMC2208 and TMC2209) in UART mode has the limitations as outlined above.

vivian-ng, 2019-12-25:
For use of Trinamic drivers in UART mode on the MRR ESPA (which does not use I2S and therefore has fewer available pins), see this [issue](https://github.com/maplerainresearch/MRR_ESPA/issues/2).

Please feel free to join in the conversation.

luc-github, 2019-12-25:
There no software serial on esp32 because any native pin can be repurposed as hardware serial
Do you mean use expander pins for software serial? I do not think there is any plan for this

vivian-ng, 2020-01-29:
I was not very informed about the TMC2209 stepper drivers. TMC2208 has a fixed slave address, which is 0, and that means only one driver can be on the same UART port since there isn't any addressing capability. But TMC2209 allows configuration of up to four different slave addresses (0 to 3). This means up to four stepper drivers can actually share the same UART port. With @luc-github's help, I managed to get two TMC2209 drivers working on the same hardware serial on the MRR ESPA.

See this video for a quick look at how to set this up for the MRR ESPA.
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

See this [blog post](https://teck78.blogspot.com/2020/01/setting-up-tmc2209-in-uart-mode-on-mrr.html) for more details.

For the MRR ESPE, the process should basically be the same if up to four TMC2209 stepper drivers are used. To use TMC2209 stepper driver on the 5th motor, a second UART port will be needed. This means adding something like
```
Serial2.begin(115200, SERIAL_8N1, 2, 4);
```
somewhere in Marlin to set up `Serial2`. This has yet to be tested though, because I only have two TMC2209 stepper drivers at the moment, and a new order is likely to be delayed since Aliexpress is on extended Chinese New Year break due to the coronavirus.

vivian-ng, 2020-01-31:
I did a test print using TMC2209 on X and Y axes, it seems to be okay.
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

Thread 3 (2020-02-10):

Problem initializing LCD controllers

vivian-ng, 2020-02-10:
A recent phenomenon has appeared and I have not managed to find time to fully track down the problem. Out of the blue, I have not been able to get LCD controllers to work with the MRR ESPE. they were working fine, then when I power on the printer the next day, I get a blank LCD screen (only backlight) and the control board does not boot up.

The issue started with CR10 stock displays, but I recently experienced this on my RepRap full graphics smart controllers (both of them, on two different MRR ESPE boards) too. All of these controllers were working fine with their respective MRR ESPE boards previously, so I do not think it is a hardware issue. Still, if anyone experiences such an issue, please contribute information here and see how we can collectively work out what the problem is.

luc-github, 2020-02-10:
Well my CR10 died in that way
why do you think it is not hardware issue,  does reflasing FW solve issue ?

vivian-ng, 2020-02-10:
@luc-github Okay, I am in the realm of guessing now... but my suspicion is the BTN_EN1 pin, which is connected to GPIO0. My guess now is that if, somehow, the BTN_EN1 is pulled to GND by the LCD controller, it is causing the board to do into download (flash) mode, which may explain the blank screen and the board failing to boot properly.

The "clone" CR10 stock display I had just miraculously worked again. I plugged it into one of my boards, blank screen. Then, I turned the knob (rotary encoder) a bit, connected the LCD again, and suddenly, the LCD came alive.

My RepRap full graphics smart controllers are also working now. On the exact same board that was giving me problems last night.

Maybe you can try turning the knob of your LCD controller and try again? I have a print going on my other printer, so when that one is done, I will test this theory out too.

luc-github, 2020-02-10:
ho nice - I am still away from home and I do not have currently espe board neither cr10 lcd on hand - so I won't be able to test before a while

vivian-ng, 2020-02-10:
LCD is working on my stock Ender-3 display too. I guess it is really an issue with BTN_EN1 being pulled to GND (somehow) when powering up.

If anyone turns on their printer and the LCD shows a blank screen, and keeps beeping (you will also notice that your hotend and heated bed and every fan is being activated), it is likely this issue. Quickly power off the printer. Then turn the LCD knob a bit. Then power on again. That should solve the problem if it is really an issue with BTN_EN1 (aka GPIO0) being pulled unintentionally to GND during boot up.

luc-github, 2020-02-10:
could this lead to fry the IO expanders like I got,  if not powered off quickly enough?

vivian-ng, 2020-02-10:
@luc-github

> could this lead to fry the IO expanders like I got, if not powered off quickly enough?

This should not happen, since this is exactly the scenario when flashing firmware via USB. I will also add a note that the firmware should not be flashed via USB when the heated bed and hotend are connected. If firmware must be flashed in such situations, the 5V_SEL jumper should be set to VUSB, and the main power supply to board and heated bed should be turned off.

Closed 2020-02-10.

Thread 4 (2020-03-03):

Babystepping and linear advance on I2S stepper stream

vivian-ng, 2020-03-03:
As of today, babystepping and linear advance does not work on I2S stepper stream. In Marlin, the pins file for the MRR ESPE will `#undef LINEAR_ADVANCE`, and if you try to do babystepping on the LCD, it will trigger a reset.

According to this [comment](https://github.com/simon-jouet/ESP32Controller/issues/10#issuecomment-590452781),
> @vivian-ng I think the problem with both is that when using I2S, the "real" stepper ISR (see https://github.com/MarlinFirmware/Marlin/blob/1955eea1b8f13697259e0e2403d47279d2d1ac6a/Marlin/src/module/stepper.cpp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) never gets called but only `Stepper::pulse_phase_isr()` and `Stepper::block_phase_isr()` (see https://github.com/MarlinFirmware/Marlin/blob/1955eea1b8f13697259e0e2403d47279d2d1ac6a/Marlin/src/HAL/HAL_ESP32/i2s.cpp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) whenever new steps are needed to fill the I2S buffer.
> One would probably have to add the logic to call `advance_isr()` and `babystepping_isr()` there, too. Unfortunately it does not seem like an easy task on first sight since one probably needs a good understanding of the stepper timings to be able to succeed

I don't think anyone other than @simon-jouet, the author of the Marlin ESP32 HAL's I2S code, has that kind of good understanding of the I2S stepper timing to be able to resolve this. So it may take a while for this issue to be resolved. Of course, the good thing about open source software is that anyone is free to give a try at finding a solution to this. Feel free to use this thread for discussions on this, and hopefully, a report of success somewhere in the future.

simon-jouet, 2020-03-04:
@vivian-ng Sorry I didn't get back to most message, I've been out of this for a while, far too many other things to do.

Linear advance and baby stepping are indeed currently not supported, when I wrote the I2S code it was just a proof of concept and that pretty much where it remained.

The code for I2S stepping is fairly straightforward there is a *lot* of it that can be abstracted away. You can pretty much abstract away the entire i2s.cpp and only consider that there is a ring buffer of steps. IIRC the stream is configured to run at 250khz to make each step 4us.

So each entry in the ring buffer represent 4us, if the bit is set to 1 then it's going to send a step to the driver for 4us if it's 0 it's not. And you just need to keep the buffer full all the time.

In the current code the stepper ISR is entirely disabled and we use the notification that one of the buffer in the ring has been consumed to plan the next ~4000 steps (here a step is a discrete 4us time period not a stepper step)

baby stepping is probably just adding an entry at the end of the buffer. For Linear advance i'm not too sure because I haven't had a look, but I guess it's just about the same, just need to schedule the steps when they are needed.

P.S: I'm doing this from memory so I might be forgetting something

vivian-ng, 2020-03-05:
@simon-jouet Thank you for chipping into the discussion. I think anyone attempting to implement this will need both an understanding of the I2S code (in terms of how it deals with the stepper pulses) and more importantly, how is babystepping and linear advance and other stuff in `stepper_isr()` implemented. Understanding the I2S code is probably the easy part, since it was written by one person; the code in `stepper.cpp` is really a challenge to figure out because many people have contributed to the code over the years.

Maybe we should post a FR in Marlin repo to see if anyone wants to give it a try.

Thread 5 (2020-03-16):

TODO List

vivian-ng, 2020-03-16:
This is a list of TODO items for the MRR ESPE.

- ~~Fix wrong RX and TX (flipped) pins on AUX1 connector~~ (done; v0.5rev1)
- Redo TMC CS pin header to allow for easy TMC SPI and UART configuration
- Add additional pins for 5V, 3.3V, and VIN

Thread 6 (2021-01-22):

Abnormal temperature display, 23 ℃ without inserting temperature sensor

dream111119, 2021-01-22:
Hello, I have trouble using MRR espe today. I use a 100k thermistor. Configure. H chooses to use a temperature sensor. The serial number is 1. But when I pulled out the temperature sensor, the temperature was 23 degrees. I checked the resistance configuration and so on, and there was no problem. I want to know the reason, and then how to solve it? thank you

vivian-ng, 2021-01-22:
@dream111119 I have this issue too. It has to do with the ESP32's ADC and we have not found a way to get it to display any value lower than 20+ degC. You can see the discussion here on [this thread](https://github.com/simon-jouet/ESP32Controller/issues/10). So there will be a "baseline" value of 20+ degC even if the thermistor is not connected. Usually, the hotend and heated bed should heat up to a temperature higher than this "baseline" temperature within the stipulated thermal runaway time.

Try heating your hotend to 200 degC and heated bed to 50 degC to see if there is any problem when the temperature goes above 23 degC.

dream111119, 2021-01-22:
Thank you. I haven't found a way to check the data of esp32-adc. When it is lower than 23 degrees, the output ADC value is the same as when it is 23 degrees. I plan to test the ADC separately. It is estimated that there will be no harvest. It's very hard

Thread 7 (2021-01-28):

When IO0 is connected to CR10 display screen, the reset will be invalid

dream111119, 2021-01-28:
Hello, I have trouble using IO0. I can't use the reset function. After clicking reset, I didn't enter the main program. Is there any way for IO0?

luc-github, 2021-01-28:
if IO0 is connected to ground at start, the board go to flash mode (https://github.com/espressif/esptool/wiki/ESP32-Boot-Mode-Selection#gpio0)  - if you use IO0 be sure it is not connected to GND at start or your board will not start

vivian-ng, 2021-01-28:
@dream111119 Please see if this [related issue](https://github.com/maplerainresearch/MRR_ESPE/issues/3) helps. Sometimes, the control knob on the LCD pulls the BTN_ENC1 to GND, which causes a problem for the ESP32.

If the reset button on the main board works, it could be an issue with the LCD controller itself. Make sure the connections from the LCD are properly connected to their required connectors on the main board.

vivian-ng, 2021-01-31:
@dream111119 If the issue is resolved, please share with everyone what was done to resolve the issue so that others with such an issue next time can try.

vivian-ng, 2021-03-22:
Closed due to no further response.

Closed 2021-03-22.

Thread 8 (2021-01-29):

Use of additional serial ports

dream111119, 2021-01-29:
Hello, I want to know how to open the second serial port? The best is serial port 1, I need to use a serial port touch screen here, thank you

dream111119, 2021-01-29:
After I opened it, the compilation passed, but actually it was useless. Do you want to know that it was like this? It's very painful

vivian-ng, 2021-01-29:
@dream111119 Please provide more information about your exact setup so that we can better understand the issue. For example, what board are you using? What LCD controller? What are the pins you are trying to use? Are you using TMC stepper drivers in UART mode? What have you actually defined in Configuration.h and Configuration_adv.h, and have you made any changes to the pins file?

dream111119, 2021-01-29:
First: I use bigtree tft35, which is a serial screen
Second: the screen works the same as online printing. I use serial port 1 to connect it.
Third: the screen itself is normal
Question: I opened serial in configuration. h SERIAL_PORT_2(1), and in pins_ MRR_ESPE.h is turned on in HARDWARE_SERIAL1_TX and HARDWARE_SERIAL1_RX, found unable to use

dream111119, 2021-01-29:
The click driver is A4988. Normal operation

luc-github, 2021-01-29:
Unfortunalty Marlin allows only 2 Serial_ports
For ESP32
One is for USB or any serial output but only one can be used at once USB is first if anything is connected if I am not wrong
One is for WIFI communication

if you can access to RX1/TX1 pins of board which are not on serial header - and configure SERIAL_PORT_2 1 - you will loose WiFi feature

On my MRR_ESPE + BTT TFT I use the Serial header  for TFT,  BTT TFT has a feature that disconnect serial of TFT and so allow to switch to USB serial

vivian-ng, 2021-01-29:
@dream111119
Try connecting the TFT35's TFT connector to AUX1 on MRR ESPE.
TFT -> MRR ESPE
5V -> 5V
GND -> GND
RX -> TX
TX -> RX

For RST on the TFT, you can connect to the RST pin on the MRR ESPE's LCD connector.

In `Configuration.h` this setting should allow you to use the AUX1 connector of MRR ESPE to communicate with TFT35 via serial. It will share the same serial as the microUSB connector on the board so you cannot use TFT35 if you have the MRR ESPE connected to a computer (like PC or Raspberry Pi) via USB.

```
#define SERIAL_PORT 0

/**
 * Select a secondary serial port on the board to use for communication with the host.
 * :[-1, 0, 1, 2, 3, 4, 5, 6, 7]
 */
//#define SERIAL_PORT_2 -1

/**
 * This setting determines the communication speed of the printer.
 *
 * 250000 works in most cases, but you might try a lower speed if
 * you commonly experience drop-outs during host printing.
 * You may try up to 1000000 to speed up SD file transfer.
 *
 * :[2400, 9600, 19200, 38400, 57600, 115200, 250000, 500000, 1000000]
 */
#define BAUDRATE 115200
```

luc-github, 2021-01-29:
@vivian-ng in latest Marlin you must now uncomment manually `#define SERIAL_PORT_2 -1` to get wifi working

vivian-ng, 2021-01-29:
> @vivian-ng in latest Marlin you must now uncomment manually `#define SERIAL_PORT_2 -1` to get wifi working

Thanks @luc-github for pointing this out.

dream111119, 2021-01-29:
Thank you very much, but I have two more questions.
First: for esp32, if I connect BTT TFT, can I open serial port 1 or serial port 2? Or reuse to other pins
Second: #define SERIAL_PORT_2 -1  have to be defined like this?

vivian-ng, 2021-01-29:
@dream111119
You should be able to set specific pins for Serial1 by:
```
#define HARDWARE_SERIAL1_RX                 21
#define HARDWARE_SERIAL1_TX                 22
```
in `Configuration.h` or `Configuration_adv.h`. Just put these lines anywhere, and replace 21 and 22 with the pins you want to use. You can then use Serial1.

But like what @luc-github said, if you, if you do
```
#define SERIAL_PORT_2 1
```
them you will not be able to use Wifi. So it is either TFT35 in serial mode, or Wifi. You may need to choose if you want to use Serial1.

But if you are using MRR ESPE and BTT TFT35, you should be able to use EXP3 connector on BTT TFT35 (connect to LCD connector on MRR ESPE) for the controller in LCD12864 emulator mode. Then, in `Configuration.h`, just:
```
#define CR10_STOCKDISPLAY
```
will do. Personally, I use Ender-3 stock display with MRR ESPE using the EXP3 connector. I have also tried with BTT TFT35 E3 V3.0 using EXP3 too. It works if you use the LCD12864 emulator mode.

vivian-ng, 2021-01-31:
@dream111119 If the issue is resolved, please share with everyone what was done to resolve the issue so that others with such an issue next time can try.

vivian-ng, 2021-03-22:
Closed due to no further feedback.

Closed 2021-03-22.

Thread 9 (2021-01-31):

TMC2130 cannot connect

dream111119, 2021-01-31:
Hello, thank you for your guidance last time. I solved the problem of TFT screen. But when I test tmc2130, I find that it can't be used. I send the M122 command, but the return is not OK. I use bigtree tech tmc2130 v3.0
1. I'm in pins_ MRR_ESP32 Turn on the chip selection pin of motor drive , and the jumper cap on the hardware is connected correctly
2. I set it in configuration. h   #define X_DRIVER_TYPE  TMC2130

dream111119, 2021-01-31:
Question: first, do I have any missing settings?
Second, will tmc2130 use the same SPI as SD card?
Third, can tmc5160 be used normally?

dream111119, 2021-01-31:
@vivian-ng

vivian-ng, 2021-01-31:
@dream111119 Please provide more information, such as the actual output from M122, and the relevant portions of Configuration.h and Configuration_adv.h so that people can better understand what the issue is.

dream111119, 2021-01-31:
M122 output:   Testing X connection... Error: All LOW
configuration.h: #define X_DRIVER_TYPE  TMC2130
configuration_adv.h:No change
pins_MRR_RSPE.h:  open #define X_CS_PIN   21
I only use it on the x-axis

dream111119, 2021-01-31:
@vivian-ng

vivian-ng, 2021-01-31:
For a start, please see the [manual](https://github.com/maplerainresearch/MRR_ESPE/blob/master/MRR%20ESPE%20manual.pdf) which contains basic information about the jumpers and wiring that is required for using TMC2130. It also contains information about how to set the CS pins in the configuration files.

The TMC2130 will share the SPI with the microSD card. Please also note this issue [here](https://github.com/maplerainresearch/MRR_ESPE/issues/1#issuecomment-574941070).

dream111119, 2021-01-31:
I did it according to the manual and also referred to the manual of motor drive, but I still couldn't do it. It's embarrassing. M122 is still a connection failure

dream111119, 2021-01-31:
@vivian-ng

vivian-ng, 2021-01-31:
@dream111119 Is the board and motor powered by VIN (12-24V)? If you are using only USB power (5V), the stepper drivers are not powered and you get connection error.

vivian-ng, 2021-01-31:
@dream111119 Also, I think the place to define the CS pins should be in `Configuration_adv.h` now. In addition to the steps in the [MRR ESPE manual](https://github.com/maplerainresearch/MRR_ESPE/blob/master/MRR%20ESPE%20manual.pdf), please also check the [Marlin documentation](https://marlinfw.org/docs/hardware/tmc_drivers.html) on how to enable TMC2130.

The MRR ESPx series of boards are experimental prototypes and assumes that the user has prior knowledge working with other 3D printer boards (like RAMPS) and Marlin. Otherwise, the learning curve can be quite steep. It is also good to take things in stages. Like first, get the board up and running with a basic setup (single hotend, no heated bed, one fan, A4988 stepper drivers). Once you can get it running a basic setup, then slowly add stuff (like LCD controller, TMC stepper drivers, more controllable fans, NeoPixels, etc.) This was basically my approach too when working on this board.

vivian-ng, 2021-03-22:
Closed due to no further response.

Closed 2021-03-22.

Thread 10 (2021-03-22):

Thermistor temperature is not correct

RobertoRmz, 2021-03-22:
I have problems with the Extruder Ntc 3950 100k Thermistor, it s**hows a different temperature to that of a digital thermometer**, the following image shows some tests that I did changing the sensors available in Marlin and the results that I obtained. I did this as well by changing the MOTHERBOARD [MMR ESPA and MMR ESPE] option in Marlin as they drive the same thermistor pin on the ESP32.

These tests were carried out with a digital thermometer that read 25.5 ° C, option 332 was the option that was closest to the thermometer temperature of 4 degrees difference.

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

However, another problem that I found with option 332 was that it no longer drops more than 29.5 ° C, even though I place a fan, an ice no longer goes down, it always stays at 29.5 ° C.

Also change values of the following Marlin options to see if there was a different value in temperature, but nothing happened:
1- #define MAX_REDUNDANT_TEMP_SENSOR_DIFF 10
2- #define TEMP_HYSTERESIS 3

I would appreciate any advice in which you could help me so that the thermistor can measure the temperature correctly.

vivian-ng, 2021-03-22:
@RobertoRmz Please see this [issue](https://github.com/maplerainresearch/MRR_ESPE/issues/6). It has to do with the ESP32's ADC. Try thermistor option 1, then heat the hotend to a slightly higher temperature (100 degC?) to see if there is a significant difference between thermistor reading and digital thermometer reading. There is actually no real solution to fix this right now for idle (room) temperature, the only solution is to see if the temperature difference at operating temperature (around 200 degC for hotend, 60+ degC for heated bed) affects printing.

RobertoRmz, 2021-03-22:
@vivian-ng thank you very much for the help, if I read [Known issue Abnormal temperature display, 23 ℃ without inserting temperature sensor] but I had not understood, but you already made it clear to me by telling me that there is no real solution to fix this right now for ambient temperature.

i did the test as you said i heated to 200 degC and using option 1 on marlin sensors and it worked fine.

I do not recommend measuring with a digital thermometer because there is a lot of temperature difference. What I did was connect the Ramps 1.4 to use only the Thermistor and place it in the Aluminum Heater Block where the ESP32 thermistor is, send it to heat to 200 degC and the results were the same, again thank you very much for the help vivian-ng, regards.

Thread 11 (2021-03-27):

Homing Problems

RobertoRmz, 2021-03-27:
Whenever I do Homing either on the X, Y or Homing on all axes, it is always the same problem.
**First the Z axis motor advances**, then the X-Y motor advances a little and it marks this error.

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

So that this error does not appear when I do Homing in the X or Y axis, the Z axis motor moves and then the X-Y, but if I quickly press the Limit Switches it does not mark that error.

It cannot be a Hardware error (Bad connections made) because when sending M119 to detect the state of the Limit Switches, it recognizes them correctly:

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

I think that some more configuration must be missing so that I can do the Homing correctly, in configuration.h in El Marlin 2.0, I have the following configuration:

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

Probe enabling and disabling the ENDSTOPPULLUPS and I keep getting the same result

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

This configuration works perfectly for me but using Arduino Mega with the Ramps 1.4 in the Marlin 1.1.X using the Core XY configuration, but in the ESP32 it does not work for me, there is another place where I can configure the Limit Switches so that it can work correctly, I would appreciate help a lot.

vivian-ng, 2021-03-28:
@RobertoRmz I am not really sure what the issue is. Are you using Marlin 1.1.x or Marlin 2.0.x? There are many differences in the configuration files between 1.1.x and 2.0.x, so a configuration that works for 1.1.x will likely not work for 2.0.x. Also, ESP32 needs to use Marlin 2.0.x, and even within 2.0.x, the configuration files have changed significantly during the past year. Some features have been renamed.

To make sure that this is not a Marlin issue, please try using an older release of Marlin 2.0.x from the releases [here](https://github.com/MarlinFirmware/Marlin/releases). I think 2.0.3 should work. You will need to work through the configuration files (Configuration.h and Configuration_Adv.h) to edit them for your setup because these two files have changed significantly over the past year. If 2.0.3 works, then try the next newer release to see if it works. Eventually, you should come to a release version that doesn't work, and that should provide information on the changes in configuration files (and firmware) that could have caused some issues.

Another troubleshooting method that I always use (besides falling back to older releases) is to start with a basic setup. A4988 stepper drivers, cartesian printer, physical endstops, etc. If the most basic setup works, then I slowly add features (s curve acceleration, TMC drivers, corexy, etc.) one by one to see which could be the feature that is giving a problem.

Also, try with Marlin 2.0.x on your RAMPS 1.4 board. If your setup can work in Marlin 1.1.x but not in 2.0.x, you may want to try searching around the Marlin repo to see if someone else has experienced the same issue. Cannot really compare Marlin 1.1.x running on RAMPS 1.4 with Marlin 2.0.x on ESP32. Too many factors have changed for proper comparison.

RobertoRmz, 2021-03-30:
I was using Marlin 1.1.X because I was using Ramps 1.4, but I have been reading about the newer 32-bit printers and they have mentioned that they have more processing power and therefore better print quality.

I am configuring ESP32 with Marlin 2.0.X in Visual Studio Code with PlatformIO and testing with Driver A4988.

I managed to solve the problem, the only thing I did was change the ESP32 for a new one and the Homing worked correctly, with Limit Switch on the x-axis and y-axis.

  In the Z Axis I put an inductive sensor at the beginning I struggled a lot because I got this error "_**#error" Z_SAFE_HOMING is recommended when homing with a probe. Enable it or comment out this line to continue.**_ ", I solved this by uncommenting **#define Z_SAFE_HOMING.** . @vivian-ng Thank you very much again for your help, many regards.

Closed 2021-03-30.

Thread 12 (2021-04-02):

Hotend temperature is not stable

RobertoRmz, 2021-04-02:
Make prints at 205, 210,215 and 225 deg, However, when printing the same problem always happens. The HotEnd temperature varies widely **± 15 deg**. It must be the PID values, these values were obtained from Pronterface's AutoTune, the values with which I made the last print were the following:

**_a)	Kp = 10.59
b)	Ki = 1.70
c)	Kd = 16.52_**

I show two temperature graphs from when I printed in Octoprint, it is possible to observe how there are very high temperature peaks:

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

I have been testing various values in the PID but still with no success. Some advice to be able to determine the correct values Kp, Ki and Kd so that the temperature of the hotend can be kept stable like the hot bed.

vivian-ng, 2021-04-02:
`M303 C10 E0 S200`
Replace the `200` in `S200` with whatever is your usual hotend printing temperature. This should print out the PID values after going through 10 cycles.

`M303 C10 E0 S200 U1`
if you want to apply the PID settings immediately after the autotune is completed.

Remember to use `M500` to save the PID values. Else they disappear upon reset/power down.
[PID autotune](https://marlinfw.org/docs/gcode/M303.html)

Another thing to note is that temperature reading values can be easily affected by EM noise. Should not be too much of an issue if you used the right capacitors for filtering.

Trying looking at the [issues here](https://github.com/simon-jouet/ESP32Controller/issues) to see if anything looks like what you are experiencing. That design is the original base design for control boards based on the ESP32.

vivian-ng, 2021-04-02:
Closing as this is an issue arising from a breadboard configuration and not the MRR ESPE board.

Closed 2021-04-02.

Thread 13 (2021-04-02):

LCD screen problem

RobertoRmz, 2021-04-02:
After assembling the printer thanks to the diagram provided by maplerainresearch, although I made some changes because it did not have many of the components of the diagram, for example to turn on the hot bed, hotend and fan, use Mosfet Irf3205.

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

It worked and I was able to print the Calibration Cube 20x20 mm, more tests need to be done to calibrate it so that it can print perfectly.

I need to connect the screen. Connect 12864 lcd full graphic smart controller that already has SD module, present the following problem:

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

The first thing I did was investigate the pins on the screen (EXP1 and EXP2) to know where to connect it on the ESP32

LCD screen: https://reprap.org/wiki/RepRapDiscount_Full_Graphic_Smart_Controller
Pin Diagram: https://reprap.org/mediawiki/images/5/51/RRD_FULL_GRAPHIC_SMART_CONTROLER_SCHEMATIC.pdf

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

Connect the display pins EXP1, EXP2 according to the pins that appear in pins_MRR_ESPE.

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

According to this information, make a diagram of how to connect the screen with the ESP32, I did it on a different breadboard than the one in the photo I put at the beginning.

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

As I show in the diagram there are 4 pins in EXP2 that I did not know where to connect it to the ESP32 **_"It may be that that is the error"._**

In the Marlin configuration enable the following 2 options “**#define SDSUPPORT** and in CONTROLLER TYPE: Graphical 128x64 (DOGM) **#define REPRAP_DISCOUNT_FULL_GRAPHIC_SMART_CONTROLLER**. I would appreciate some advice so that the screen can work properly.

vivian-ng, 2021-04-02:
@RobertoRmz
See schematic [here](https://github.com/maplerainresearch/MRR_ESPE/tree/master/adapters/LCD_adapter).

Info on how to use LCD12864 was posted [here](https://github.com/maplerainresearch/MRR_ESPE/issues/1#issuecomment-567368605) and [here](https://teck78.blogspot.com/2019/12/the-lcd-connector-on-mrr-espe-which-is.html). You can always search the issues to see if something has already been written instead of opening a new issue.

vivian-ng, 2021-04-02:
@RobertoRmz
Also, please note that this board was not designed to be used on a breadboard. It is hard to provide any help unless you are using a proper PCB, since a breadboard setup can have other types of errors like loose connections, broken wires, and EMI that is different from what the PCB version has.

vivian-ng, 2021-04-02:
Closing as this is an issue arising from a breadboard configuration and not the MRR ESPE board.

Closed 2021-04-02.

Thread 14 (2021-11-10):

Generic I2S questions

petervanderwalt, 2021-11-10:
Hi!.  I am experimenting with TMC5161 drivers, on a breadboard setup running an ESP32 with the I2S expanders.

I have just about everything else working, i can control dumb drivers just fine, but I don't seem to be getting the CS pin to switch for spi transactions to the TMCs.

Verified with a scope, activity on SCK and MOSI, but CS just stays high. Do you know if

a) its possible to use on of the I2S expansion pins as a CS pin for the Trinamics (no spare GPIOs on the ESP32, and I know Esp32_Grbl can use the I2S pins as CS pins for TMC and

b) any pointers on making it work?

M122 reports ALL HIGH so I know its a comms issue, and not seeing CS go low at the start of the transaction makes me suspicious of whether I can use I2S CS pins in Marlin?

Also, can I run more than 32 bits? For example, can I run 6* 595s for 48 extra Outputs?

vivian-ng, 2021-11-10:
I am afraid I have never tried using TMC5161 drivers before so I am not able to provide any help on this. Hopefully someone else who has tried this wanders here and sees these questions. Will leave this issue open in case someone else can provide more insights.

petervanderwalt, 2021-11-11:
Thanks for getting back to me (:

Shout if you'd like a set I am sure I can arrange some for you (:

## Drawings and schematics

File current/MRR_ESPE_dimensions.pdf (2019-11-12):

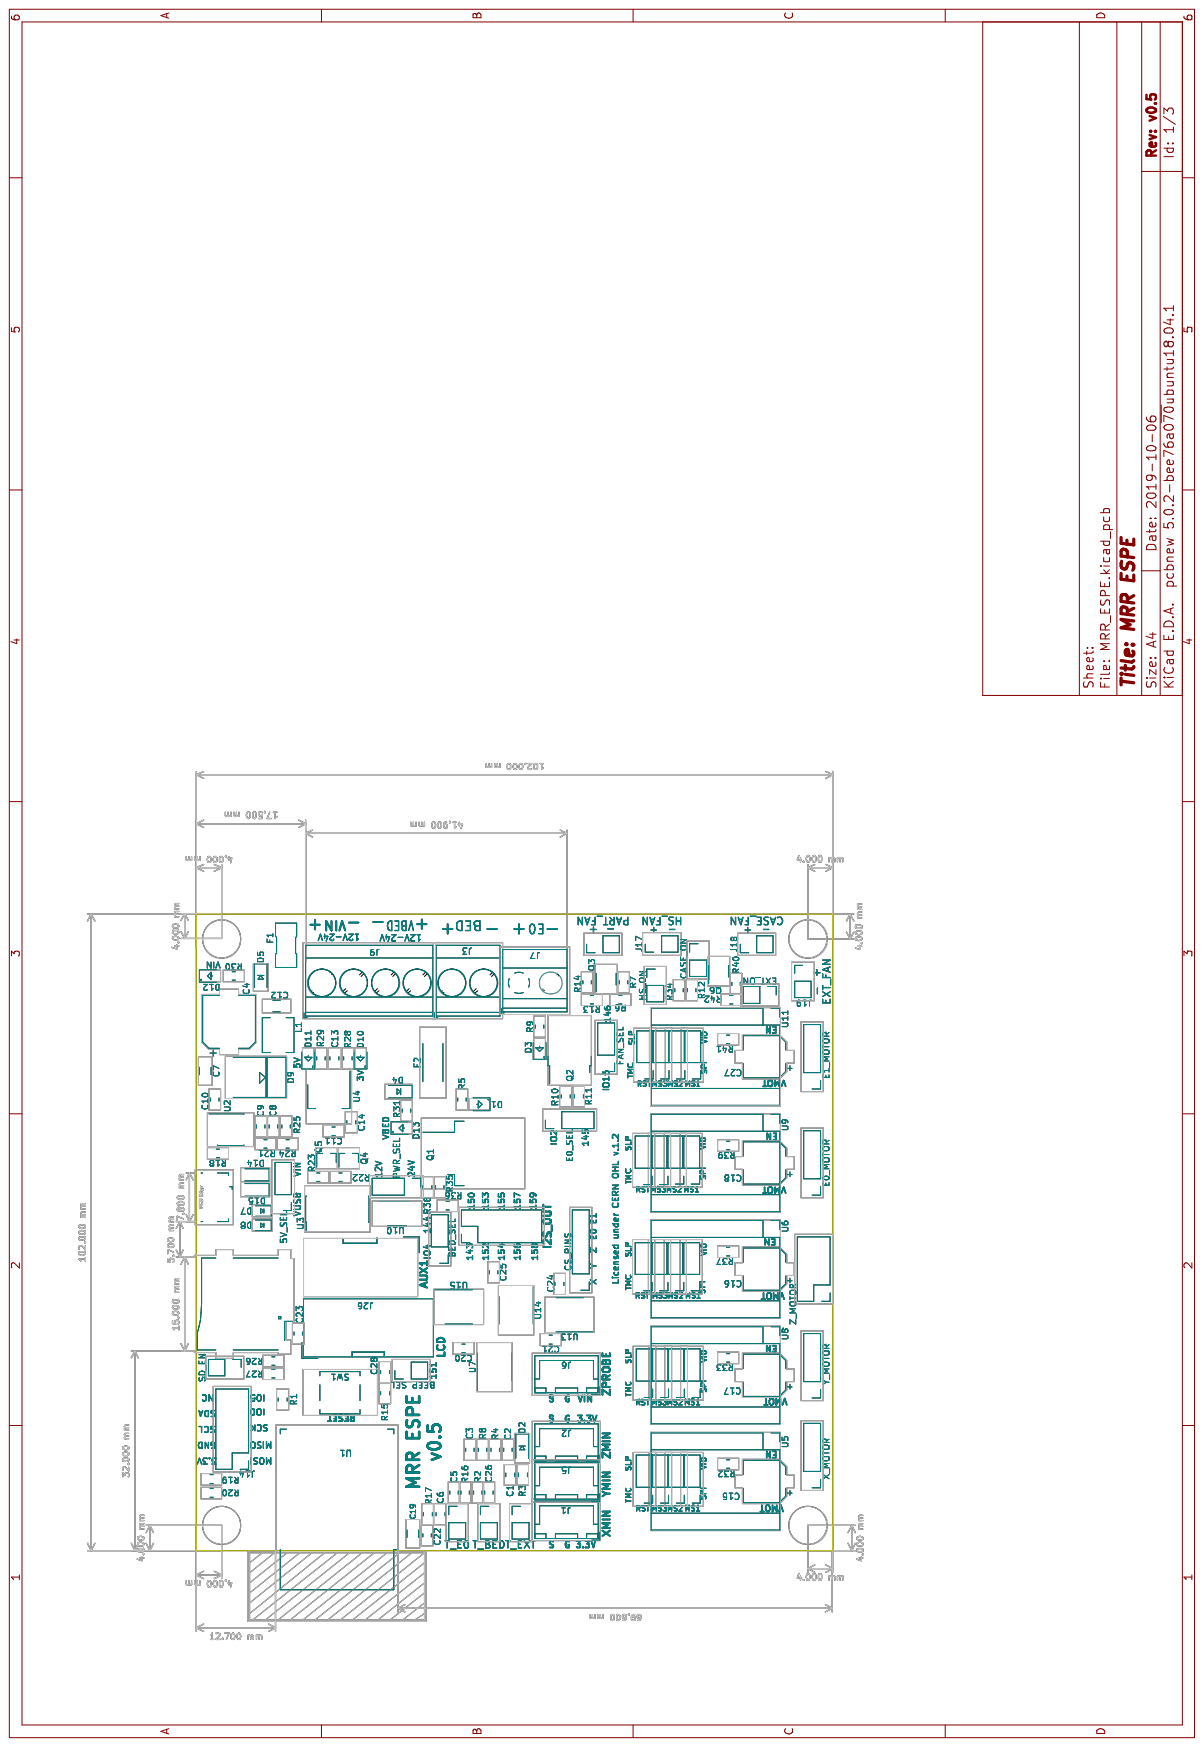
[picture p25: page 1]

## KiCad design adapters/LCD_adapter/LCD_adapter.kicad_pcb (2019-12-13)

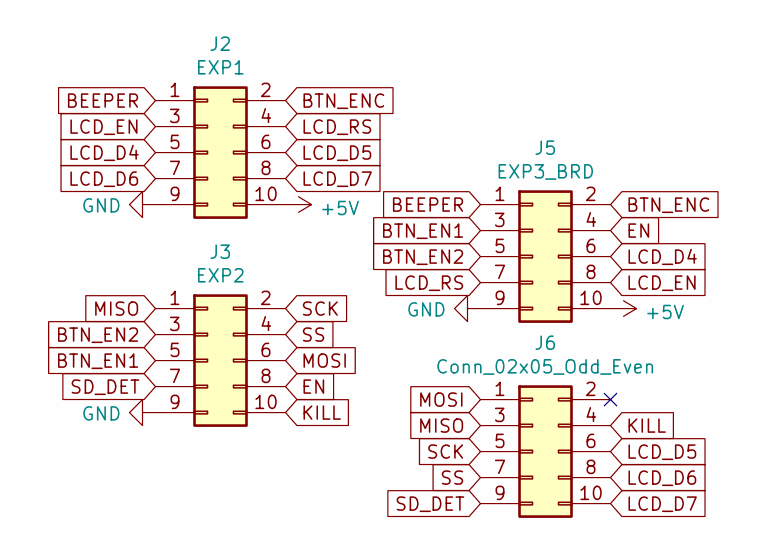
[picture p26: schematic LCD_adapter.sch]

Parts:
J2: EXP1; IDC-Header_2x05_P2.54mm_Vertical
J3: EXP2; IDC-Header_2x05_P2.54mm_Vertical
J5: EXP3_BRD; IDC-Header_2x05_P2.54mm_Vertical
J6: Conn_02x05_Odd_Even; PinHeader_2x05_P2.54mm_Vertical

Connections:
+5V: J2.10, J5.10
BEEPER: J2.1, J5.1
BTN_EN1: J3.5, J5.3
BTN_EN2: J3.3, J5.5
BTN_ENC: J2.2, J5.2
EN: J3.8, J5.4
GND: J2.9, J3.9, J5.9
KILL: J3.10, J6.4
LCD_D4: J2.5, J5.6
LCD_D5: J2.6, J6.6
LCD_D6: J2.7, J6.8
LCD_D7: J2.8, J6.10
LCD_EN: J2.3, J5.8
LCD_RS: J2.4, J5.7
MISO: J3.1, J6.3
MOSI: J3.6, J6.1
SCK: J3.2, J6.5
SD_DET: J3.7, J6.9
SS: J3.4, J6.7

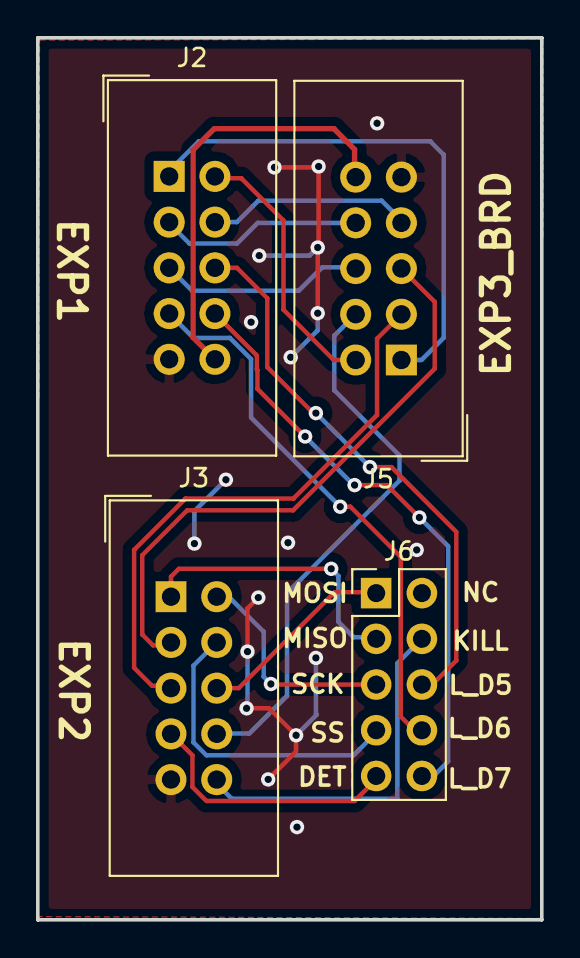
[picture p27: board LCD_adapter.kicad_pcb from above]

Board: 2 copper layers, 28.0 x 49.0 mm, 4 parts (0 on the bottom side), 19 nets.

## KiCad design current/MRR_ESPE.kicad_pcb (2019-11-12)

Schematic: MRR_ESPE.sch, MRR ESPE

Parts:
C1, C2, C3, C20, C21, C23, C24, C25, C28: 100nF25V; C_0805_2012Metric; Mfg part no. 0805B104K250; LCSC Part Number C128353
C4: 100uF50V; CP_Elec_8x10; Mfg part no. VEJ101M1HTR-0810; LCSC Part Number C176665
C5, C6, C22, C26: 22uF6.3V; C_0805_2012Metric; Mfg part no. CL21A226MQQNNNE; LCSC Part Number C5674
C7: 4.7uF50V; C_1206_3216Metric; Mfg part no. CL31B475KBHNFNE; LCSC Part Number C307575
C8: 820pF50V; C_0805_2012Metric; Mfg part no. 0805B821K500CT; LCSC Part Number C152862
C9: 56pF50V; C_0805_2012Metric; Mfg part no. 0805N560J500CT; LCSC Part Number C296102
C10: 100nF50V; C_0805_2012Metric; Mfg part no. GCM21BR71H104KA37L; LCSC Part Number C161260
C11: 1nF16V; C_0805_2012Metric; Mfg part no. 0805B103K500NT; LCSC Part Number C52278
C12: 47uF10V; C_1206_3216Metric; Mfg part no. LMK316BJ476ML-T; LCSC Part Number C92821
C13, C14: 47uF6.3V; C_0805_2012Metric; Mfg part no. JMK212BJ476MG-T; LCSC Part Number C87159
C15, C16, C17, C18, C27: 100uF35V; CP_Elec_6.3x7.7; Mfg part no. CS1V101M-CRE77; LCSC Part Number C97811
C19: 100uF6.3V; C_1206_3216Metric; Mfg part no. CL31A107MQHNNNE; LCSC Part Number C15008
D1: LED_BED; LED_0805; Mfg part no. 17-21SURC/S530-A3/TR8; LCSC Part Number C72037
D2: 1N4148W; D_SOD-123; Mfg part no. 1N4148W; LCSC Part Number C81598
D3: LED_E0; LED_0805; Mfg part no. 17-21SURC/S530-A3/TR8; LCSC Part Number C72037
D4, D5: 1N4007W; D_SOD-123F; Mfg part no. 1N4007W; LCSC Part Number C108803
D7, D8: PESD5V0S1BA; D_SOD-323; Mfg part no. PESD5V0S1BA,115; LCSC Part Number C19224
D9: B540C-13-F; D_SMC; Mfg part no. B540C-13-F; LCSC Part Number C72264
D10: LED_3V; LED_0805; Mfg part no. 17-21SYGC/S530-E2/TR8; LCSC Part Number C73548
D11: LED_5V; LED_0805; Mfg part no. 17-21SYGC/S530-E2/TR8; LCSC Part Number C73548
D12: LED_VIN; LED_0805; Mfg part no. 17-21/BHC-XL2M2TY/3T; LCSC Part Number C72035
D13: LED_VBED; LED_0805; Mfg part no. 17-21/BHC-XL2M2TY/3T; LCSC Part Number C72035
D14, D15: 1N5819W; D_SOD-123; Mfg part no. 1N5819W; LCSC Part Number C169540
F1: 15A 2410; Littelfuse_0451; Mfg part no. 0451015.MRL; LCSC Part Number C44480
F2: 30A 3912; Littelfuse_0456; Mfg part no. 0456030.ER; LCSC Part Number C187558
H1, H2, H3, H4: MountingHole; MountingHole_3.2mm_M3_DIN965
J1: X_MIN; JST_XH_B03B-XH-A_1x03_P2.50mm_Vertical; Mfg part no. B3B-XH-A(LF)(SN); LCSC Part Number C144394
J2: Z_MIN; JST_XH_B03B-XH-A_1x03_P2.50mm_Vertical; Mfg part no. B3B-XH-A(LF)(SN); LCSC Part Number C144394
J3: BED; TerminalBlock_Phoenix_MKDS-3-2-5.08_1x02_P5.08mm_Horizontal; Mfg part no. MKDS3/2-5.08; LCSC Part Number C89120
J4: Micro_SD_Card_China; Conn_uSDcard; Mfg part no. TF-15×15; LCSC Part Number C111196
J5: Y_MIN; JST_XH_B03B-XH-A_1x03_P2.50mm_Vertical; Mfg part no. B3B-XH-A(LF)(SN); LCSC Part Number C144394
J6: Z_PROBE; JST_XH_B03B-XH-A_1x03_P2.50mm_Vertical; Mfg part no. B3B-XH-A(LF)(SN); LCSC Part Number C144394
J7: E0; TerminalBlock_Phoenix_MKDS-1,5-2-5.08_1x02_P5.08mm_Horizont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; Mfg part no. MKDSN1.5/2-5.08; LCSC Part Number C91153
J8: T_EXT; PinHeader_1x02_P2.54mm_Vertical; Mfg part no. C124375; LCSC Part Number C124375
J9: PWR_IN; TerminalBlock_Phoenix_MKDS-3-4-5.08_1x04_P5.08mm_Horizontal; Mfg part no. MKDS3/4-5.08; LCSC Part Number C90087
J10: PART_FAN; PinHeader_1x02_P2.54mm_Vertical; Mfg part no. C124375; LCSC Part Number C124375
J11: UNUSED; PinHeader_2x05_P2.54mm_Vertical; Mfg part no. C124387; LCSC Part Number C124387
J12: T_BED; PinHeader_1x02_P2.54mm_Vertical; Mfg part no. C124375; LCSC Part Number C124375
J13: T_E0; PinHeader_1x02_P2.54mm_Vertical; Mfg part no. C124375; LCSC Part Number C124375
J14: I2C/SPI; PinHeader_2x05_P2.54mm_Vertical; Mfg part no. C124387; LCSC Part Number C124387
J15: AUX1; IDC-Header_2x04_P2.54mm_Vertical; Mfg part no. C9135; LCSC Part Number C9135
J16: USB_B_Micro; USB_Micro-B_Molex-105017-0001; Mfg part no. 105017-0001; LCSC Part Number C136000
J17: HS_FAN; PinHeader_1x02_P2.54mm_Vertical; Mfg part no. C124375; LCSC Part Number C124375
J18: CASE_FAN; PinHeader_1x02_P2.54mm_Vertical; Mfg part no. C124375; LCSC Part Number C124375
J19: EXT_FAN; PinHeader_1x02_P2.54mm_Vertical; Mfg part no. C124375; LCSC Part Number C124375
J20: CS_PINS; PinHeader_1x05_P2.54mm_Vertical; Mfg part no. C124379; LCSC Part Number C124379
J21: X_MOTOR; PinHeader_1x04_P2.54mm_Vertical; Mfg part no. C124378; LCSC Part Number C124378
J22: Z_MOTOR; PinHeader_2x04_P2.54mm_Vertical; Mfg part no. C124386; LCSC Part Number C124386
J23: Y_MOTOR; PinHeader_1x04_P2.54mm_Vertical; Mfg part no. C124378; LCSC Part Number C124378
J24: E0_MOTOR; PinHeader_1x04_P2.54mm_Vertical; Mfg part no. C124378; LCSC Part Number C124378
J25: E1_MOTOR; PinHeader_1x04_P2.54mm_Vertical; Mfg part no. C124378; LCSC Part Number C124378
J26: EXP3; IDC-Header_2x05_P2.54mm_Vertical; Mfg part no. C5665; LCSC Part Number C5665
JP1: X_MS1; PinHeader_1x03_P2.54mm_Vertical; Mfg part no. C124376; LCSC Part Number C124376
JP2: Y_MS1; PinHeader_1x03_P2.54mm_Vertical; Mfg part no. C124376; LCSC Part Number C124376
JP3: Z_MS1; PinHeader_1x03_P2.54mm_Vertical; Mfg part no. C124376; LCSC Part Number C124376
JP4: E0_MS1; PinHeader_1x03_P2.54mm_Vertical; Mfg part no. C124376; LCSC Part Number C124376
JP5: X_MS2; PinHeader_1x03_P2.54mm_Vertical; Mfg part no. C124376; LCSC Part Number C124376
JP6: Y_MS2; PinHeader_1x03_P2.54mm_Vertical; Mfg part no. C124376; LCSC Part Number C124376
JP7: Z_MS2; PinHeader_1x03_P2.54mm_Vertical; Mfg part no. C124376; LCSC Part Number C124376
JP8: E0_MS2; PinHeader_1x03_P2.54mm_Vertical; Mfg part no. C124376; LCSC Part Number C124376
JP9: X_MS3; PinHeader_1x03_P2.54mm_Vertical; Mfg part no. C124376; LCSC Part Number C124376
JP10: Y_MS3; PinHeader_1x03_P2.54mm_Vertical; Mfg part no. C124376; LCSC Part Number C124376
JP11: Z_MS3; PinHeader_1x03_P2.54mm_Vertical; Mfg part no. C124376; LCSC Part Number C124376
JP12: E0_MS3; PinHeader_1x03_P2.54mm_Vertical; Mfg part no. C124376; LCSC Part Number C124376
JP13: X_RST; PinHeader_1x03_P2.54mm_Vertical; Mfg part no. C124376; LCSC Part Number C124376
JP14: Y_RST; PinHeader_1x03_P2.54mm_Vertical; Mfg part no. C124376; LCSC Part Number C124376
JP15: Z_RST; PinHeader_1x03_P2.54mm_Vertical; Mfg part no. C124376; LCSC Part Number C124376
JP16: E0_RST; PinHeader_1x03_P2.54mm_Vertical; Mfg part no. C124376; LCSC Part Number C124376
JP17: BEEP_SEL; PinHeader_1x02_P2.54mm_Vertical; Mfg part no. C124375; LCSC Part Number C124375
JP18: BED_SEL; PinHeader_1x03_P2.54mm_Vertical; Mfg part no. C124376; LCSC Part Number C124376
JP19: FAN_SEL; PinHeader_1x03_P2.54mm_Vertical; Mfg part no. C124376; LCSC Part Number C124376
JP20: E0_SEL; PinHeader_1x03_P2.54mm_Vertical; Mfg part no. C124376; LCSC Part Number C124376
JP21: HS_ON; PinHeader_1x02_P2.54mm_Vertical; Mfg part no. C124375; LCSC Part Number C124375
JP22: E1_MS1; PinHeader_1x03_P2.54mm_Vertical; Mfg part no. C124376; LCSC Part Number C124376
JP23: CASE_ON; PinHeader_1x02_P2.54mm_Vertical; Mfg part no. C124375; LCSC Part Number C124375
JP24: EXT_ON; PinHeader_1x02_P2.54mm_Vertical; Mfg part no. C124375; LCSC Part Number C124375
JP25: E1_MS2; PinHeader_1x03_P2.54mm_Vertical; Mfg part no. C124376; LCSC Part Number C124376
JP26: E1_MS3; PinHeader_1x03_P2.54mm_Vertical; Mfg part no. C124376; LCSC Part Number C124376
JP27: E1_RST; PinHeader_1x03_P2.54mm_Vertical; Mfg part no. C124376; LCSC Part Number C124376
JP28: 5V_SEL; PinHeader_1x03_P2.54mm_Vertical; Mfg part no. C124376; LCSC Part Number C124376
JP29: SD_EN; PinHeader_1x02_P2.54mm_Vertical; Mfg part no. C124375; LCSC Part Number C124375
JP30: PWR_SEL; PinHeader_1x03_P2.54mm_Vertical; Mfg part no. C124376; LCSC Part Number C124376
L1: 4.7uH4.5A; SMMS0530; Mfg part no. SMMS0530-4R7M; LCSC Part Number C181722
Q1: IRLS3034PBF; TO-263-2
Q2: IRLR8743TRPBF; TO-252-2
Q3, Q6: WST3392; SOT-23-6_Handsoldering; Mfg part no. WST3392; LCSC Part Number C148366
Q4, Q5: S9014; SOT-23; Mfg part no. S9014; LCSC Part Number C181164
R1, R3, R4, R8, R32, R33, R37, R39, R41: 10K; R_0805_2012Metric; Mfg part no. 0805W8F1002T5E; LCSC Part Number C38522
R2, R16, R17, R19, R20: 4.7K; R_0805_2012Metric; Mfg part no. 0805W8F4701T5E; LCSC Part Number C17673
R5, R9, R30, R31: 2.2K; R_0805_2012Metric; Mfg part no. 0805W8F2201T5E; LCSC Part Number C17520
R6, R10, R12, R13, R40: 10R; R_0805_2012Metric; Mfg part no. 0805W8F100JT5E; LCSC Part Number C17415
R7, R11, R14, R34, R42: 100K; R_0805_2012Metric; Mfg part no. 0805W8F1003T5E; LCSC Part Number C149504
R15, R22, R23: 12K; R_0805_2012Metric; Mfg part no. 0805W8F1202T5E; LCSC Part Number C17444
R18: 73.2K; R_0805_2012Metric; Mfg part no. WR08X7322FTL; LCSC Part Number C170958
R21: 23.7K; R_0805_2012Metric; Mfg part no. WR08X2372FTL; LCSC Part Number C170848
R24: 60.4K; R_0805_2012Metric; Mfg part no. RC0805FR-0760K4L; LCSC Part Number C273994
R25: 11.5K; R_0805_2012Metric; Mfg part no. 0805W8F1152T5E; LCSC Part Number C17418
R26, R27: 0R; R_0805_2012Metric; Mfg part no. 0805W8F0000T5E; LCSC Part Number C17477
R28: 220R; R_0805_2012Metric; Mfg part no. 0805W8F2200T5E; LCSC Part Number C17557
R29, R36: 330R; R_0805_2012Metric; Mfg part no. 0805W8F3300T5E; LCSC Part Number C17630
R35, R38: 1K; R_0805_2012Metric; Mfg part no. 0805W8F1001T5E; LCSC Part Number C17513
SW1: RESET; 6x6mmTactileSwitch; Mfg part no. K2-6639SP-C4SC-04; LCSC Part Number C83206
U1: ESP32-WROOM-32D; ESP32-WROOM-32; Mfg part no. ESP32-WROOM-32; LCSC Part Number C95209
U2: TPS54340DDA; TI_SO-PowerPAD-8_ThermalVias; Mfg part no. TPS54340DDAR; LCSC Part Number C45886
U3: CH340C; SOIC-16_3.9x9.9mm_P1.27mm; Mfg part no. CH340C; LCSC Part Number C84681
U4: AMS1117-3.3; SOT-223-3_TabPin2; Mfg part no. AMS1117-3.3; LCSC Part Number C6186
U5, U6, U8, U9, U11: Pololu_board; Pololu_Breakout-16_15.2x20.3mm; Mfg part no. x2; LCSC Part Number C27438
U7, U13, U14, U15: 74HCT595; TSSOP-16_4.4x5mm_P0.65mm; Mfg part no. MC74HCT595ADTR2G; LCSC Part Number C152276
U10: TLP182; MFSOP6-4_4.4x3.6mm_P1.27mm; Mfg part no. TLP182(GB-TPL,E; LCSC Part Number C96457

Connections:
5V1: C12.2, D14.2 (A), L1.2, R24.1
+3V3: C11.2, C14.1, C19.1, C22.1, C23.1, J1.1, J2.1, J4.4 (VDD), J5.1, J14.2, JP1.3 (B), JP2.3 (B), JP3.3 (B), JP4.3 (B), JP5.3 (B), JP6.3 (B), JP7.3 (B), JP8.3 (B), JP9.3 (B), JP10.3 (B), JP11.3 (B), JP12.3 (B), JP22.3 (B), JP25.3 (B), JP26.3 (B), R1.1, R2.1, R3.2, R4.2, R8.2, R15.1, R16.1, R17.1, R19.2, R20.2, R28.2, R32.1, R33.1, R37.1, R39.1, R41.1, U1.2 (VDD), U3.4 (V3), U3.16 (VCC), U4.2 (VO), U5.10 (+5V), U6.10 (+5V), U7.10 (~SRCLR), U8.10 (+5V), U9.10 (+5V), U11.10 (+5V), U13.10 (~SRCLR), U14.10 (~SRCLR), U15.10 (~SRCLR)
+5V: C13.1, C20.2, C21.2, C24.2, C25.2, J15.1, J15.2, J26.10, JP28.2 (C), R29.2, U4.3 (VI), U7.16 (VCC), U13.16 (VCC), U14.16 (VCC), U15.16 (VCC)
/D+: D8.1 (A1), J16.3 (D+), U3.5 (UD+)
/D-: D7.1 (A1), J16.2 (D-), U3.6 (UD-)
BED_EXT_IN: JP18.2 (C), R36.1
BEEPER_PIN: J26.1, JP17.1
BTN_EN1: J14.7, J26.3, Q5.3 (C), R1.2, U1.25 (IO0)
BTN_EN2: J26.5, U1.14 (IO12)
BTN_ENC: J26.2, U1.13 (IO14)
COMP: C9.1, R21.1, U2.6 (COMP)
DTR: Q5.2 (E), R22.2, U3.13 (~DTR)
E0_CS: J20.4, JP12.1 (A)
E0_MS1: JP4.2 (C), U9.2 (MS1)
E0_MS2: JP8.2 (C), U9.3 (MS2)
E0_MS3: JP12.2 (C), U9.4 (MS3)
E0_RST: JP16.2 (C), U9.5 (~RST)
E0_SLP: JP16.3 (B), U9.6 (~SLEEP)
E1_CS: J20.5, JP26.1 (A)
E1_MS1: JP22.2 (C), U11.2 (MS1)
E1_MS2: JP25.2 (C), U11.3 (MS2)
E1_MS3: JP26.2 (C), U11.4 (MS3)
E1_RST: JP27.2 (C), U11.5 (~RST)
E1_SLP: JP27.3 (B), U11.6 (~SLEEP)
EN: C28.1, J26.4, Q4.3 (C), R15.2, SW1.2, U1.3 (EN)
FB: R24.2, R25.1, U2.5 (FB)
GND: C1.1, C2.1, C3.1, C4.2, C5.1, C6.1, C7.1, C8.2, C9.2, C11.1, C12.1, C13.2, C14.2, C15.2, C16.2, C17.2, C18.2, C19.2, C20.1, C21.1, C22.2, C23.2, C24.1, C25.1, C26.1, C27.2, C28.2, D5.2 (A), D7.2 (A2), D8.2 (A2), D9.2 (A), D10.1 (K), D11.1 (K), D12.1 (K), J1.2, J2.2, J4.6 (VSS), J5.2, J6.2, J8.2, J9.2, J12.2, J13.2, J14.4, J15.3, J15.4, J16.5 (GND), J16.6 (Shield), J26.9, JP21.2, JP23.2, JP24.2, Q2.3 (S), Q3.2, Q3.5, Q6.2, Q6.5, R7.1, R11.1, R14.1, R18.1, R25.2, R34.1, R42.1, SW1.1, U1.1 (GND), U1.15 (GND), U1.38 (GND), U1.39, U2.7 (GND), U2.9 (GNDPAD), U3.1 (GND), U4.1 (GND), U5.9 (GND), U5.15 (GND), U6.9 (GND), U6.15 (GND), U7.8 (GND), U7.13 (~OE), U8.9 (GND), U8.15 (GND), U9.9 (GND), U9.15 (GND), U10.3, U11.9 (GND), U11.15 (GND), U13.8 (GND), U13.13 (~OE), U14.8 (GND), U14.13 (~OE), U15.8 (GND), U15.13 (~OE)
GNDD: D4.2 (A), D13.1 (K), J9.3, Q1.3 (S), R35.1
HEATER_BED: JP18.1 (A), U1.26 (IO4)
HEATER_E0: JP20.1 (A), U1.24 (IO2)
I2S_BCK: U1.10 (IO25), U7.11 (SRCLK), U13.11 (SRCLK), U14.11 (SRCLK), U15.11 (SRCLK)
I2S_DATA: U1.12 (IO27), U7.14 (SER)
I2S_WS: U1.11 (IO26), U7.12 (RCLK), U13.12 (RCLK), U14.12 (RCLK), U15.12 (RCLK)
IO5: J14.9, JP29.1, U1.29 (IO5)
IO34: C26.2, J8.1, R2.2, U1.6 (IO34)
LCD_PINS_D4: J26.6, U1.27 (IO16)
LCD_PINS_EN: J26.8, U1.28 (IO17)
LCD_PINS_RS: J26.7, U1.16 (IO13)
MISO: J4.7 (DAT0), J14.3, JP13.1 (A), JP14.1 (A), JP15.1 (A), JP16.1 (A), JP27.1 (A), U1.31 (IO19)
MOSI: J4.3 (CMD), J14.1, JP1.1 (A), JP2.1 (A), JP3.1 (A), JP4.1 (A), JP22.1 (A), U1.37 (IO23)
unnamed: C8.1, R21.2
unnamed: C10.1, D9.1 (K), L1.1, U2.8 (SW)
unnamed: C10.2, U2.1 (BOOT)
unnamed: D1.1 (K), J3.2, Q1.2 (D)
unnamed: D1.2 (A), R5.1
unnamed: D2.1 (K), J6.3
unnamed: D3.1 (K), J7.2, Q2.2 (D)
unnamed: D3.2 (A), R9.1
unnamed: D10.2 (A), R28.1
unnamed: D11.2 (A), R29.1
unnamed: D12.2 (A), R30.1
unnamed: D13.2 (A), R31.1
unnamed: D14.1 (K), JP28.3 (B)
unnamed: D15.1 (K), JP28.1 (A)
unnamed: F1.2, J9.1
unnamed: F2.2, J9.4
unnamed: J10.2, Q3.6
unnamed: J17.2, JP21.1, Q3.4
unnamed: J18.2, JP23.1, Q6.6
unnamed: J19.2, JP24.1, Q6.4
unnamed: J21.1, U5.14 (2B)
unnamed: J21.2, U5.13 (2A)
unnamed: J21.3, U5.12 (1B)
unnamed: J21.4, U5.11 (1A)
unnamed: J23.1, U8.14 (2B)
unnamed: J23.2, U8.13 (2A)
unnamed: J23.3, U8.12 (1B)
unnamed: J23.4, U8.11 (1A)
unnamed: J24.1, U9.14 (2B)
unnamed: J24.2, U9.13 (2A)
unnamed: J24.3, U9.12 (1B)
unnamed: J24.4, U9.11 (1A)
unnamed: J25.1, U11.14 (2B)
unnamed: J25.2, U11.13 (2A)
unnamed: J25.3, U11.12 (1B)
unnamed: J25.4, U11.11 (1A)
unnamed: JP30.1 (A), R35.2, R38.1
unnamed: JP30.3 (B), R38.2, U10.4
unnamed: Q2.1 (G), R10.1
unnamed: Q3.1, R13.1
unnamed: Q3.3, R6.1
unnamed: Q4.1 (B), R22.1
unnamed: Q5.1 (B), R23.1
unnamed: Q6.1, R12.1
unnamed: Q6.3, R40.1
unnamed: R18.2, U2.4 (RT/CLK)
unnamed: R26.2, U3.2 (TXD)
unnamed: R27.2, U3.3 (RXD)
unnamed: R36.2, U10.1
unnamed: U13.9 (QH'), U14.14 (SER)
unnamed: U7.9 (QH'), U13.14 (SER)
unnamed: U14.9 (QH'), U15.14 (SER)
PART_FAN: JP19.1 (A), U1.23 (IO15)
Q128: R32.2, U5.1 (EN), U7.15 (QA)
Q129: U5.7 (STEP), U7.1 (QB)
Q130: U5.8 (DIR), U7.2 (QC)
Q131: R33.2, U7.3 (QD), U8.1 (EN)
Q132: U7.4 (QE), U8.7 (STEP)
Q133: U7.5 (QF), U8.8 (DIR)
Q134: R37.2, U6.1 (EN), U7.6 (QG)
Q135: U6.7 (STEP), U7.7 (QH)
Q136: U6.8 (DIR), U13.15 (QA)
Q137: R39.2, U9.1 (EN), U13.1 (QB)
Q138: U9.7 (STEP), U13.2 (QC)
Q139: U9.8 (DIR), U13.3 (QD)
Q140: R41.2, U11.1 (EN), U13.4 (QE)
Q141: U11.7 (STEP), U13.5 (QF)
Q142: U11.8 (DIR), U13.6 (QG)
Q143: J11.1, U13.7 (QH)
Q144: JP18.3 (B), U14.15 (QA)
Q145: JP20.3 (B), U14.1 (QB)
Q146: JP19.3 (B), U14.2 (QC)
Q147: R12.2, R34.2, U14.3 (QD)
Q148: R6.2, R7.2, U14.4 (QE)
Q149: R40.2, R42.2, U14.5 (QF)
Q150: J11.2, U14.6 (QG)
Q151: JP17.2, U14.7 (QH)
Q152: J11.3, U15.15 (QA)
Q153: J11.4, U15.1 (QB)
Q154: J11.5, U15.2 (QC)
Q155: J11.6, U15.3 (QD)
Q156: J11.7, U15.4 (QE)
Q157: J11.8, U15.5 (QF)
Q158: J11.9, U15.6 (QG)
Q159: J11.10, U15.7 (QH)
RTS: Q4.2 (E), R23.2, U3.14 (~RTS)
SCK: J4.5 (CLK), J14.5, JP5.1 (A), JP6.1 (A), JP7.1 (A), JP8.1 (A), JP25.1 (A), U1.30 (IO18)
SCL: J14.6, R20.1, U1.36 (IO22)
SDA: J14.8, R19.1, U1.33 (IO21)
SS: J4.2 (DAT3/CD), JP29.2
TEMP_BED_PIN: C5.2, J12.1, R16.2, U1.5 (SENSOR_VN)
TEMP_E0_PIN: C6.2, J13.1, R17.2, U1.4 (SENSOR_VP)
TO_FAN_E0: JP19.2 (C), R13.2, R14.2
TO_HEATER_BED: JP30.2 (C), Q1.1 (G)
TO_HEATER_E0: JP20.2 (C), R10.2, R11.2
UART+: J15.8, R27.1, U1.35 (TXD0/IO1)
UART-: J15.6, R26.1, U1.34 (RXD0/IO3)
VBED: D4.1 (K), F2.1, J3.1, R5.2, R31.2, U10.6
VIN: C4.1, C7.2, C15.1, C16.1, C17.1, C18.1, C27.1, D5.1 (K), F1.1, J6.1, J7.1, J10.1, J17.1, J18.1, J19.1, R9.2, R30.2, U2.2 (VIN), U5.16 (+12V), U6.16 (+12V), U8.16 (+12V), U9.16 (+12V), U11.16 (+12V)
VUSB: D15.2 (A), J16.1 (VBUS)
X_CS: J20.1, JP9.1 (A)
X_MIN: C1.2, J1.3, R3.1, U1.7 (IO35)
X_MS1: JP1.2 (C), U5.2 (MS1)
X_MS2: JP5.2 (C), U5.3 (MS2)
X_MS3: JP9.2 (C), U5.4 (MS3)
X_RST: JP13.2 (C), U5.5 (~RST)
X_SLP: JP13.3 (B), U5.6 (~SLEEP)
Y_CS: J20.2, JP10.1 (A)
Y_MIN: C3.2, J5.3, R8.1, U1.8 (IO32)
Y_MS1: JP2.2 (C), U8.2 (MS1)
Y_MS2: JP6.2 (C), U8.3 (MS2)
Y_MS3: JP10.2 (C), U8.4 (MS3)
Y_RST: JP14.2 (C), U8.5 (~RST)
Y_SLP: JP14.3 (B), U8.6 (~SLEEP)
Z_1A: J22.7, J22.8, U6.11 (1A)
Z_1B: J22.5, J22.6, U6.12 (1B)
Z_2A: J22.3, J22.4, U6.13 (2A)
Z_2B: J22.1, J22.2, U6.14 (2B)
Z_CS: J20.3, JP11.1 (A)
Z_MIN: C2.2, D2.2 (A), J2.3, R4.1, U1.9 (IO33)
Z_MS1: JP3.2 (C), U6.2 (MS1)
Z_MS2: JP7.2 (C), U6.3 (MS2)
Z_MS3: JP11.2 (C), U6.4 (MS3)
Z_RST: JP15.2 (C), U6.5 (~RST)
Z_SLP: JP15.3 (B), U6.6 (~SLEEP)

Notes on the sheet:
Microcontroller
MicroSD card
Power
Step-down: 5V
Step-down: 3.3V
Power indicator LEDs
Power input
USB to serial
5V input protection
Heater: Bed
Heater: E0
Part-cooling fan
Stepper drivers
Thermistors
Endstops
Reset switch
Connectors
Stepper driver jumpers
CS Pins for SPI mode
Licensed under CERN OHL v1.2
Case fan
Heat sink fan
Extra fan
Selection jumpers

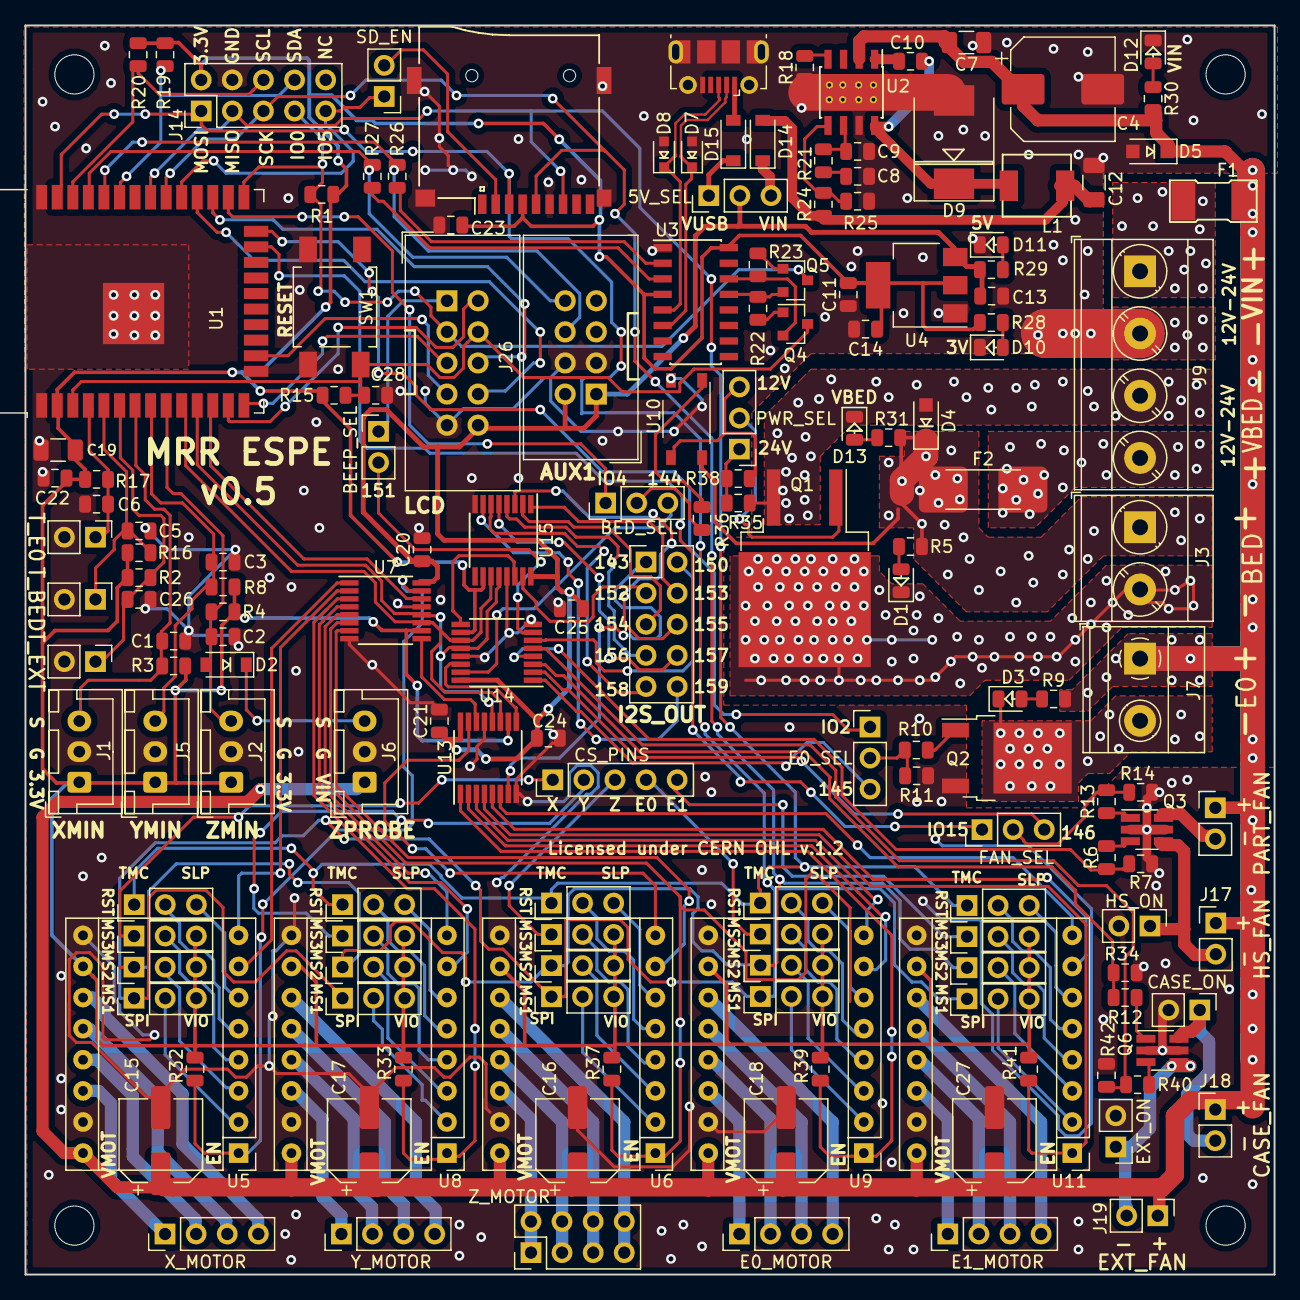
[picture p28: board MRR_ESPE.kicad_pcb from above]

Board: 2 copper layers, 102.0 x 102.0 mm, 168 parts (0 on the bottom side), 165 nets.

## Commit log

2019-05-30 Added v0.1
    [MRR_ESPE-B.Cu.gbl, MRR_ESPE-B.Mask.gbs, MRR_ESPE-B.Paste.gbp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]
2019-06-19 Added v0.2
    [MRR_ESPE-B.Cu.gbl, MRR_ESPE-B.Mask.gbs, MRR_ESPE-B.Paste.gbp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]
2019-10-10 Added v0.3 and v0.4
    [MRR_ESPE-B.Cu.gbl, MRR_ESPE-B.Mask.gbs, MRR_ESPE-B.Paste.gbp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]
2019-10-30 Added v0.5
    [MRR_ESPE-B.Cu.gbl, MRR_ESPE-B.Mask.gbs, MRR_ESPE-B.Paste.gbp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]
2019-11-03 Minor change to v0.5 silkscreen
    [MRR_ESPE-B.Cu.gbl, MRR_ESPE-B.Mask.gbs, MRR_ESPE-B.Paste.gbp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]
2019-11-12 Added cases
    [40mm_fan_cover.stl, 80mm_fan_cover.stl, ESPE_basic_bottom.stl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]
2019-11-12 Added case README
2019-11-12 Added PCB dimensions
    [MRR_ESPE.kicad_pcb]
2019-11-25 Revised small case
    [ESPE_bottom_small.stl]
2019-11-29 Updated BEEPER pin def
2019-12-08 Added v0.5rev1 to fix AUX1 issue
    [MRR_ESPE-B.Cu.gbl, MRR_ESPE-B.Mask.gbs, MRR_ESPE-B.Paste.gbp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]
2019-12-13 Added adapter boards
    [AUX1_adapter-B.Cu.gbl, AUX1_adapter-B.Mask.gbs, AUX1_adapter-B.Paste.gbp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]
